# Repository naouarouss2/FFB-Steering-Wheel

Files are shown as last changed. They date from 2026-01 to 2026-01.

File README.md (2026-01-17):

# DIY FFB Steering Wheel
## What is it ?
A Force Feedback Wheelbase is a device used in car, truck, bus, or any other 3+ wheeled vehicle (as motorcycles require something different).

The difference between it and a standard game controller is, as the name suggests : **Force Feedback**

Force Feedback is what will create a physical connection between you and the game/simulator you're playing. It will allow you to feel every bump, road imperfection, steering stiffness, vibration... as if you're driving in real life.

## Features
-  **Direct drive**, making it very silent, providing the most accurate and lossless feedback
-  **12-15Nm Force Feedback** (**5.7-7.1x** more powerful than the Logitech G29)
-  **12 Programmable buttons** (Depends on the wheel attached)
-  **Auto center**
-  **0.01125° sensitivity**, making it comparable to some high-end wheelbases on the market

## Why do I want to make it ?
I have always wanted to have a simracing setup. Whenever I go to a mall or a gaming café and see a simracing setup, I run like a kid to try it.

I once tried a professional direct drive setup with a motion setup, and this really made me more excited about simracing.

The problem is that the only decent wheelbase available in Tunisia is the Logitech G29 family. They are pretty nice, but overpriced in Tunisia, and it really didn't really fill my heart and satisfy my requirements.

So I wanted to build my own wheelbase, tweaked to my likings and preferences, with endless upgrading and tuning options.

## 3D Design
I designed everything inside Solidworks, as I am pretty familiar with it, and I already have the CSWA certification.
I divided the design in 2 parts :
-  First, the wheelbase sub-assembly :

| **Full design** | **Aluminium machined parts** | **3D Printed parts** | **Commercial parts** |
|---|---|---|---|
||||

-  Next, the steering wheel sub-assembly

| **Full design** | **Aluminium machined parts** | **3D Printed parts** | **Commercial parts** |
|---|---|---|---|
|||||

And here are pictures of the finished product !


## Wheelbase PCB
To minimize wiring and make things simpler and cleaner inside, I made a PCB for the wheelbase

| **3D View** | **PCB Routing View** | **Schematics** | 
|---|---|---|
||||

## Wiring Diagrams
### Wheelbase wiring diagram
fb58e3fb-e4d4-41d1-b4ad-96e4c3caae32
### Steering wheel wiring diagram (made on KiCad, but no PCB)


## BOM

|Type |Component name |Product description |Shop / Manufacturer |Local|URL |Unit price|Shipping|Product Amount|Product Total (excluding shipping)|Product Total (with shipping)|
|---|---|---|---|-----|---|---|---|---|---|---|
|Commercial parts |20*20mm Aluminium Profile|Used to make the wheelbase frame |Seli |Yes  |https://seli.tn/product/20x20-profile-aluminium-industriel-dk/ |15,6 |0 |1 |15,6 |15,6 |
| |40*20mm Aluminium Profile|Used to make the wheelbase frame |Seli |Yes  |https://seli.tn/product/20x40-profile-aluminium-industriel-r6/ |22,5 |0 |1 |22,5 |22,5 |
| |SK16 Brackets |Used to mount the motor in place |Seli |Yes  |https://seli.tn/product/sk16-support-d-arbre-en-aluminium-diam-16/ |3,11 |0 |2 |6,22 |6,22 |
| |UFL004 Bearings |Used to guide the shaft in rotation |Aliexpress |No |https://ar.aliexpress.com/item/1005007098430647.html |17,9 |0 |1 |17,9 |17,9 |
| |ODESC 52V Driver |Used to drive the motor and process FFB Logic |Aliexpress |No |https://ar.aliexpress.com/item/1005005763345874.html |78 |13,2 |1 |78 |91,2 |
| |STM32H743VIT6 Board |Used to control the ODESC board along with the game inputs |Aliexpress |No |https://ar.aliexpress.com/item/1005009563874211.html |11,55 |4,05 |1 |11,55 |15,6 |
| |2000PPR Rotary Encoder |Used to determine the steering wheel's position |Aliexpress |No |https://ar.aliexpress.com/item/1005004387342695.html |15,35 |7,82 |1 |15,35 |23,17 |
| |30-tooth 30mm pulley |Used to tie the encoder's shaft to the steering wheel shaft |Aliexpress |No |https://ar.aliexpress.com/item/1005008678109995.html |4,67 |0 |1 |4,67 |4,67 |
| |Quick release mechanism  |Used to mount the steering wheel to the wheelbase |Aliexpress |No |https://ar.aliexpress.com/item/1005009121231549.html |62,86 |0 |1 |62,86 |62,86 |
| |GX12 Connector kit (M/F) |Used to connect input peripherals to the wheelbase |Tunisian Smart Innovation|Yes  |https://tuni-smart-innovation.com/products/connecteur-male-et-femelle-gx12-4-broches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 |1,49 |0 |5 |7,45 |7,45 |
| |120mm Fan |Used to cool the wheelbase's electronics |2BTrading |Yes  |https://2btrading.tn/ventilateur-radiateur/2391-ventilateur-dc12v-034a-12x12x38cm.html |10,73 | |1 |10,73 |10,73 |
| |XT60M connector |Used to power the wheelbase |Cothings |Yes  |https://cothings.net/products/connecteur-amass-xt60e-m-male |1,73 |0 |1 |1,73 |1,73 |
| |Endstop switch |Game inputs |Cothings |Yes  |https://cothings.net/products/copie-de-capteur-de-temperature-thermistance-ntc-100k-ntc-mf52at-1 |0,45 |0 |2 |0,9 |0,9 |
| |Pushbutton |Game inputs |Cothings |Yes  |https://cothings.net/products/mini-bouton-poussoir-rond-a-reinitialisation-automatique-bleu-etanche-pbs-33b-12mm-2-broches |0,86 |0 |8 |6,88 |6,88 |
| |Hall effect sensor |Used to calibrate the wheel's initial position |Cothings |Yes  |https://cothings.net/products/ky-024-capteur-a-effet-hall-analogique-pour-vitesse-et-comptage |1,55 |0 |1 |1,55 |1,55 |
| |36V 500W Power supply |Used to power the wheelbase |Aliexpress |No |https://ar.aliexpress.com/item/1005003923590693.html |50,53 |10,49 |1 |50,53 |61,02 |
| |GT2-6 400mm belt |Used to connect the shaft pulley to the encoder pulley |2BTrading |Yes  |Courroie GT2-6 400mm |3 |0 |1 |3 |3 |
| |Seed XIAO RP2040 |Microcontroller for the steering wheel |Aliexpress |No |https://ar.aliexpress.com/item/1005003682505451.html |4,78 |4,52 |1 |4,78 |9,3 |
| |Steering Wheel |The actual steering wheel |Aliexpress |No |https://ar.aliexpress.com/item/1005009791304312.html |25,99 |42,53 |1 |25,99 |68,52 |
| |TJA1051 |CAN transceiver |Aliexpress |No |https://ar.aliexpress.com/item/1005005569468051.html |4,1 |0 |1 |4,1 |4,1 |
| |12V Buck Converter |Used to power the fan |Aliexpress |No |https://ar.aliexpress.com/item/1005008597548688.html |2,6 |7,28 |1 |2,6 |12,48 |
| |5V Buck Converter |Used to power the MCU and other peripherals |Aliexpress |No |https://ar.aliexpress.com/item/1005008597548688.html |2,6 | |1 |2,6 | |
| |USB-C Female Connector |Used to connect the wheelbase to the computer |Aliexpress |No |https://ar.aliexpress.com/item/1005009695057393.html |11,62 |0 |1 |11,62 |11,62 |
| |USB-C 90° cable |Used to transfer the USB connection from the PCB to the external connector|Aliexpress |No |https://ar.aliexpress.com/item/1005002708307702.html |6,4 |4,79 |1 |6,4 |11,19 |
| |USB-C Breakout Board | |Aliexpress |No |https://ar.aliexpress.com/item/1005004807492800.html |4,19 |0 |1 |4,19 |4,19 |
| |JST-XH 4 Pin Connector |Used to make cable connections easier |Tunisian Smart Innovation|Yes  |https://tuni-smart-innovation.com/products/connecteur-jst-xh2-54-4-broches-male-femelle-avec-cable-de-20-cm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 |0,7 |0 |1 |0,7 |0,7 |
| |JST-XH 3 Pin Connector |Used to make cable connections easier |Tunisian Smart Innovation|Yes  |https://tuni-smart-innovation.com/products/connecteur-jst-xh2-54-3-broches-male-femelle-avec-cable-de-20-cm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|0,62 |0 |1 |0,62 |0,62 |
| |JST-XH 2 Pin Connector |Used to make cable connections easier |Tunisian Smart Innovation|Yes  |https://tuni-smart-innovation.com/products/connecteur-jst-xh-2-broches-male-femelle-avec-cable-de-20-cm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 |0,49 |0 |1 |0,49 |0,49 |
| |M2X10 Screw |Screw diameter = 2mm, length = 10mm |Already have | |N/A |0 |0 |4 |0 |0 |
| |M3x10 Screw |Screw diameter = 3mm, length = 10mm |Already have | |N/A |0 |0 |8 |0 |0 |
| |M3x16 Screw |Screw diameter = 3mm, length = 16mm |Already have | |N/A |0 |0 |10 |0 |0 |
| |M4x8 Screw |Screw diameter = 4mm, length = 8mm |Already have | |N/A |0 |0 |8 |0 |0 |
| |M4x16 Screw |Screw diameter = 4mm, length = 16mm |Already have | |N/A |0 |0 |4 |0 |0 |
| |M5x16 Screw |Screw diameter = 5mm, length = 16mm |Already have | |N/A |0 |0 |6 |0 |0 |
| |M5x36 Screw |Screw diameter = 5mm, length = 36mm |Already have | |N/A |0 |0 |4 |0 |0 |
| |M5x50 Screw |Screw diameter = 5mm, length = 50mm |Already have | |N/A |0 |0 |6 |0 |0 |
| |M6x20 Screw |Screw diameter = 6mm, length = 20mm |Already have | |N/A |0 |0 |4 |0 |0 |
| |M10x16 Screw |Screw diameter = 10mm, length = 16mm |Already have | |N/A |0 |0 |2 |0 |0 |
| |M3 Nut |Nut diameter = 3mm |Already have | |N/A |0 |0 |4 |0 |0 |
| |M10 Nut |Nut diameter = 10mm |Already have | |N/A |0 |0 |2 |0 |0 |
| |M3 Aluminium Profile Nut |Nut for aluminium profiles, diameter = 3mm |Seli |Yes  |https://seli.tn/product/ecrou-marteau/ |0,1 |0 |4 |0,4 |0,4 |
| |M4 Aluminium Profile Nut |Nut for aluminium profiles, diameter = 4mm |Seli |Yes  |https://seli.tn/product/ecrou-marteau/ |0,1 |0 |8 |0,8 |0,8 |
| |M5 Aluminium Profile Nut |Nut for aluminium profiles, diameter = 5mm |Seli |Yes  |https://seli.tn/product/ecrou-marteau/ |0,1 |0 |4 |0,4 |0,4 |
| |M6 Aluminium Profile Nut |Nut for aluminium profiles, diameter = 6mm |Seli |Yes  |https://seli.tn/product/ecrou-marteau/ |0,1 |0 |4 |0,4 |0,4 |
| |Table clamps (x2) |Used to mount the wheelbase on the table |Aliexpress |No |https://ar.aliexpress.com/item/1005006458478718.html |47,8 |8,28 |1 |47,8 |56,08 |
| |Hoverboard motor |Used to provide force feedback |Facebook Marketplace |Yes  |N/A |19 |0 |1 |19 |19 |
| |TOTAL | | | | | | | |450,31 |553,27 |
|PCB |Wheelbase PCB |Holds the various electronic components without the need for wiring |JLC PCB |No |N/A |2 |21,91 |1 |2 |21,91 |
|Aluminium machined parts|Front plate | |JLC CNC |No |N/A |8,72 |49,48 |1 |8,72 |72,77 |
| |Back plate | |JLC CNC |No |N/A |10,63 | |1 |10,63 | |
| |Paddle (x2) | |JLC CNC |No |N/A |3,94 | |1 |3,94 | |
|GRAND TOTAL | | | | | | | | |475,6 |647,95 |

This table format above is slightly different from what I originally made, so to understand it better, I would recommend

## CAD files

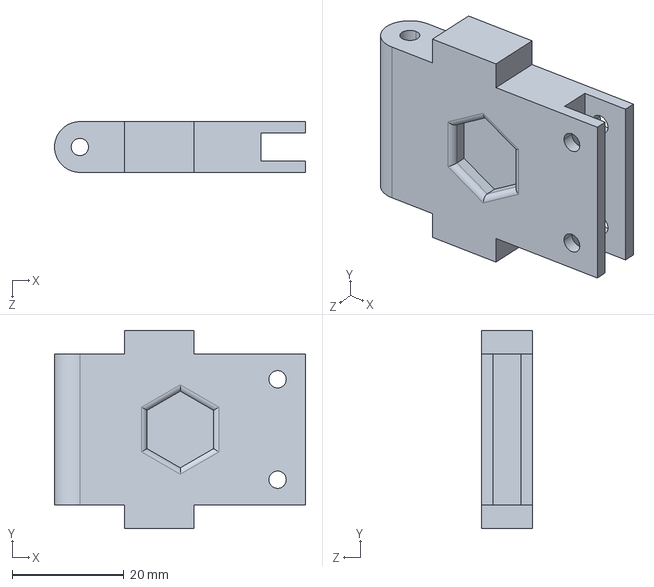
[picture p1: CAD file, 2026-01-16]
CAD/Steering Wheel/3D Printed parts/Paddle Holder.STEP
45.0 x 35.5 x 9.10 mm

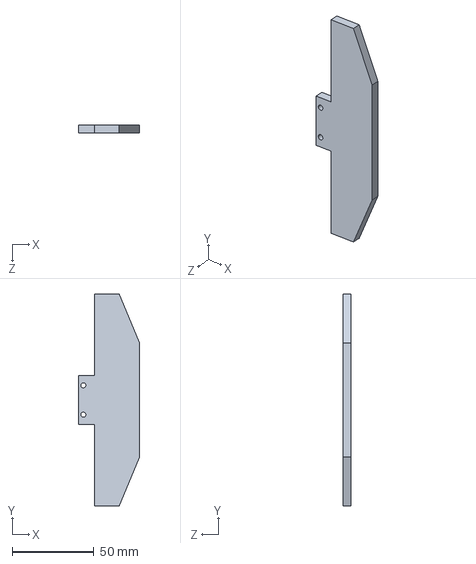
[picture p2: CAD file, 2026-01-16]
CAD/Steering Wheel/Aluminium machined parts/Paddle.STEP
37.5 x 130.0 x 5.00 mm

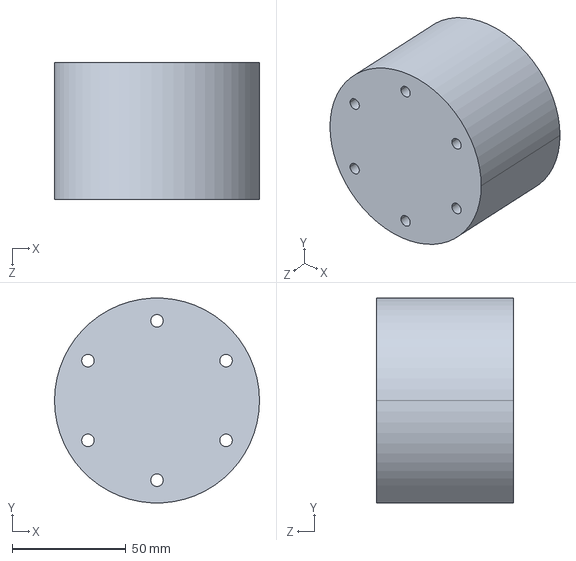
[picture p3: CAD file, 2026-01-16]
CAD/Steering Wheel/Commercial parts/QR Sample.STEP
90.0 x 89.9 x 60.0 mm

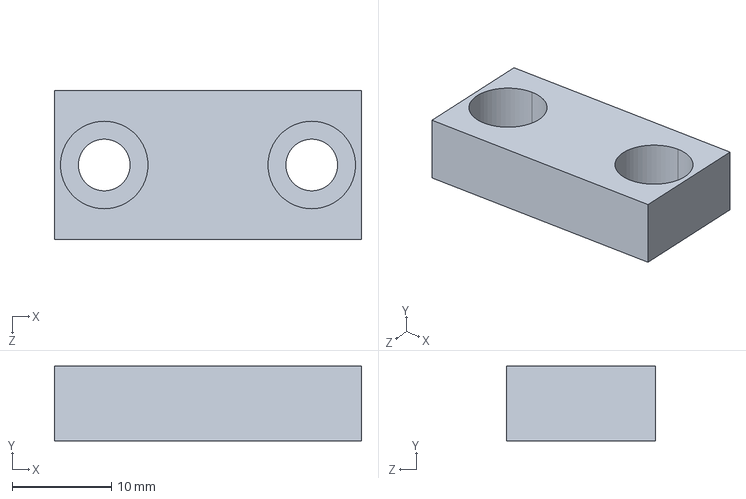
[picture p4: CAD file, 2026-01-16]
CAD/Wheelbase/3D Printed parts/Clamp Surface Flattener.STEP
30.9 x 7.50 x 15.0 mm

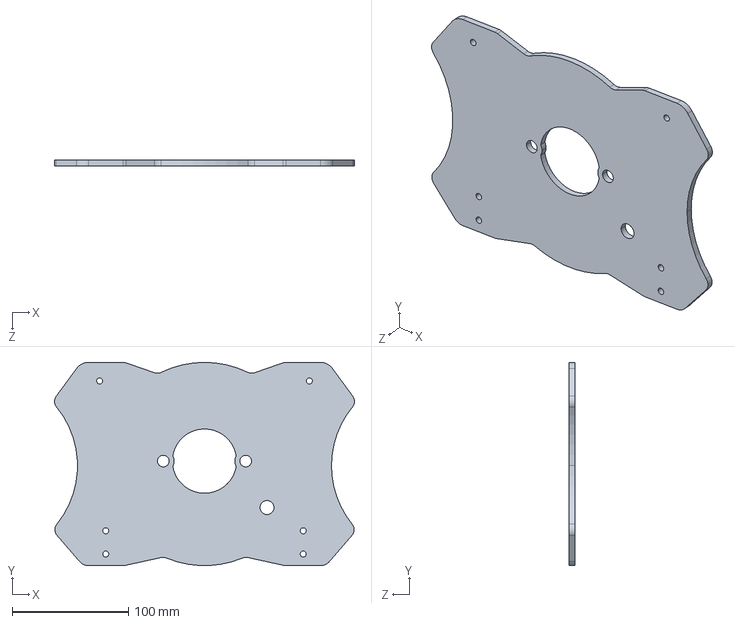
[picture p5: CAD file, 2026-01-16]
CAD/Wheelbase/Aluminium machined parts/Front plate.STEP
258.3 x 175.0 x 5.00 mm

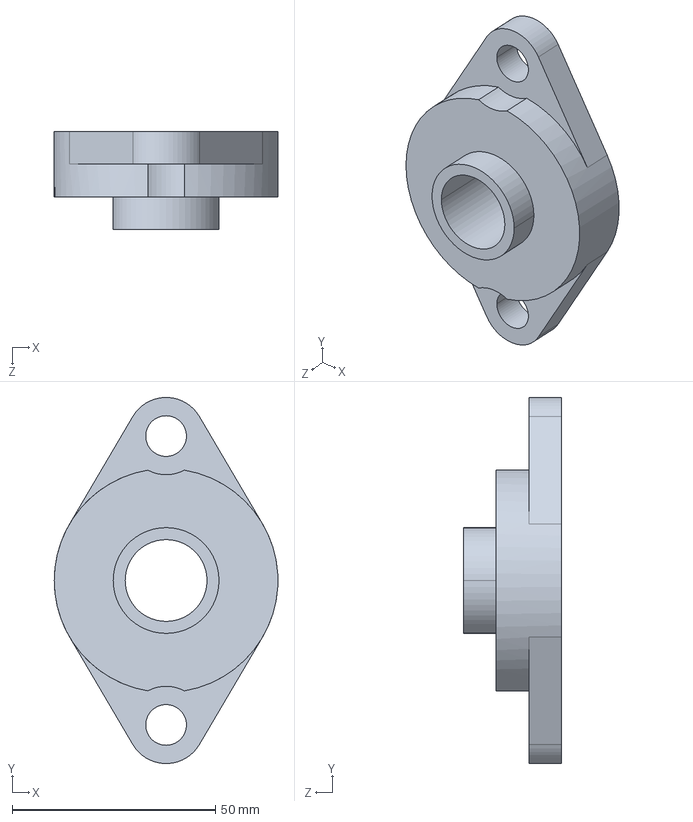
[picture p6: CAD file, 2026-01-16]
CAD/Wheelbase/Commercial parts/KFL004.STEP
55.0 x 90.0 x 24.0 mm

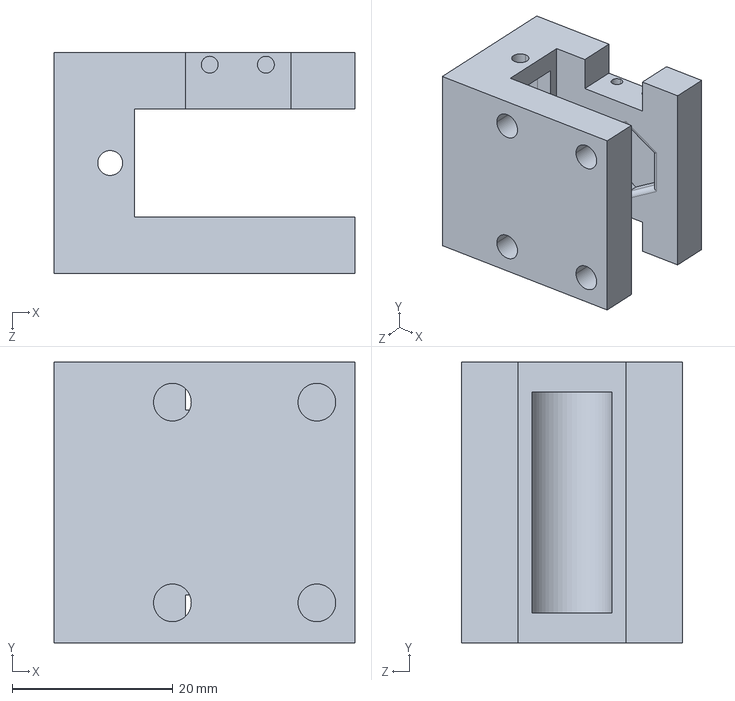
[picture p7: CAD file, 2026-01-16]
CAD/Steering Wheel/3D Printed parts/Paddle Shifter Mount.STEP
37.5 x 35.0 x 27.5 mm

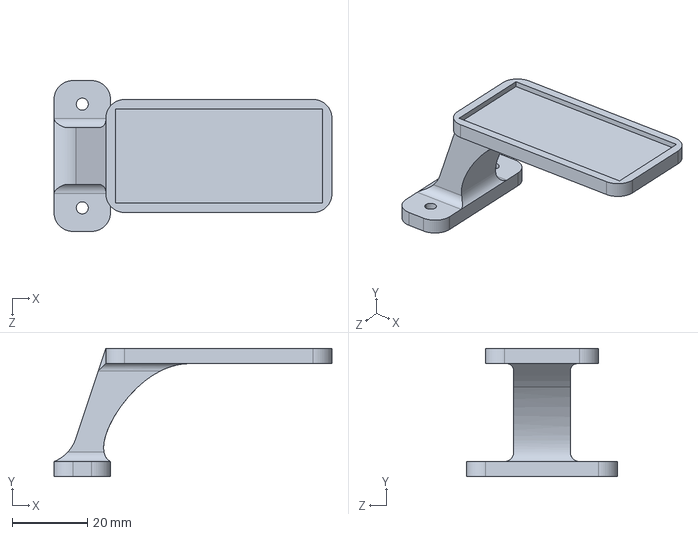
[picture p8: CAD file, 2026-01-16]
CAD/Wheelbase/3D Printed parts/Hall Eff Sensor Mount.STEP
73.8 x 34.0 x 40.0 mm

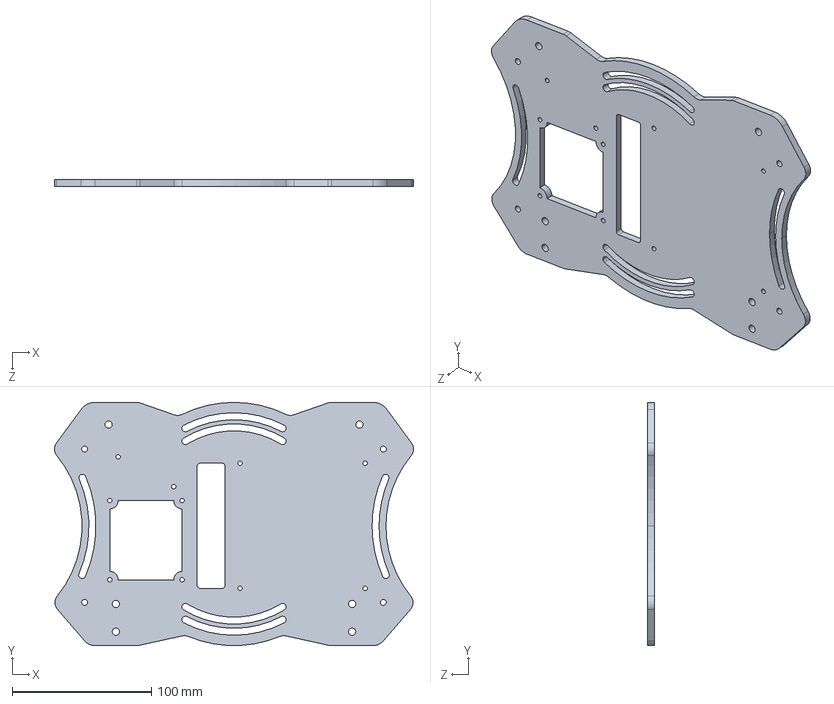
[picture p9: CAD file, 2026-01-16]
CAD/Wheelbase/Aluminium machined parts/Back plate.STEP
258.3 x 175.0 x 5.00 mm

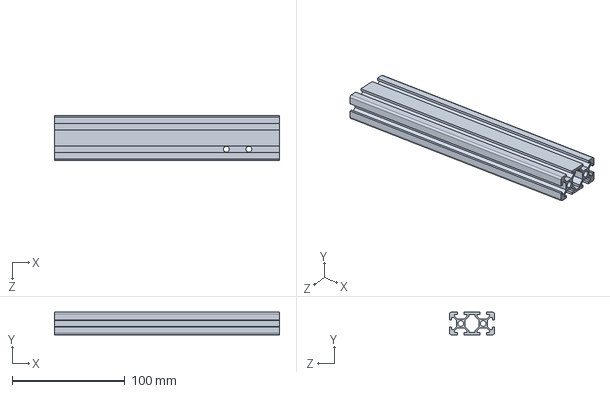
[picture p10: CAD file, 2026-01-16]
CAD/Wheelbase/Commercial parts/Side 2040 profile.STEP
200.0 x 20.0 x 40.0 mm

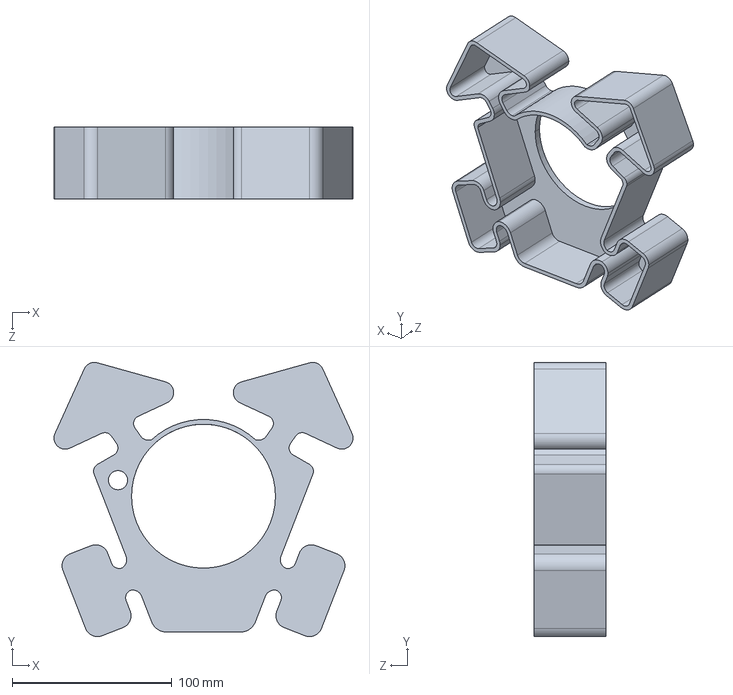
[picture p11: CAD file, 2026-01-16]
CAD/Steering Wheel/3D Printed parts/Back Enclosure.STEP
187.0 x 171.5 x 45.0 mm

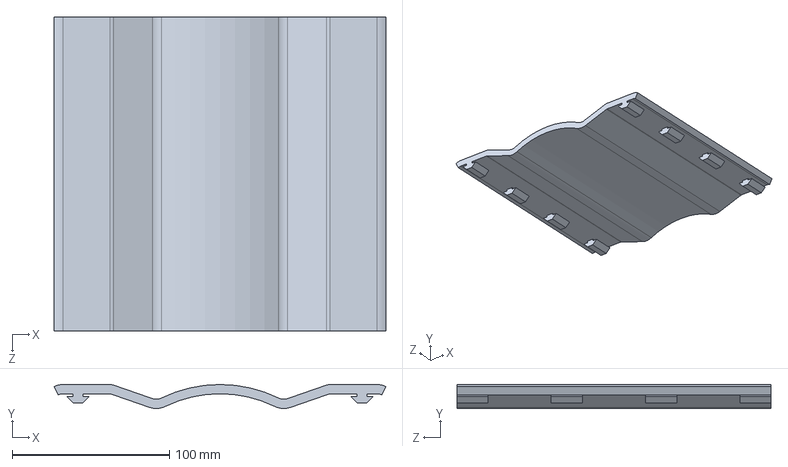
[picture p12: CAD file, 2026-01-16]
CAD/Wheelbase/3D Printed parts/Top cover.STEP
211.1 x 15.3 x 200.0 mm

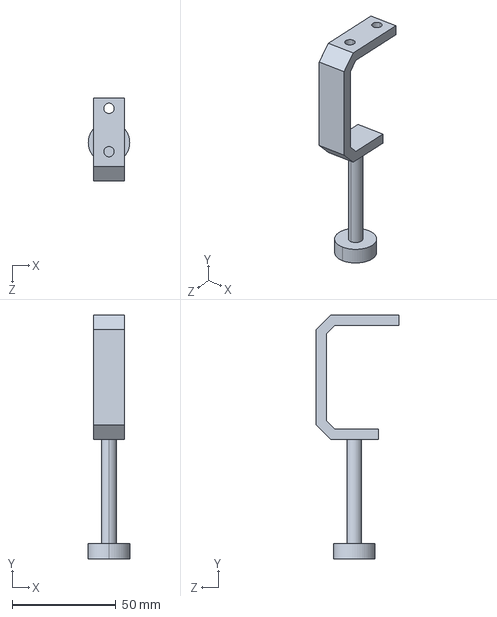
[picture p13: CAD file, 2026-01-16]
CAD/Wheelbase/Commercial parts/Clamp Sample.STEP
20.0 x 117.5 x 40.0 mm

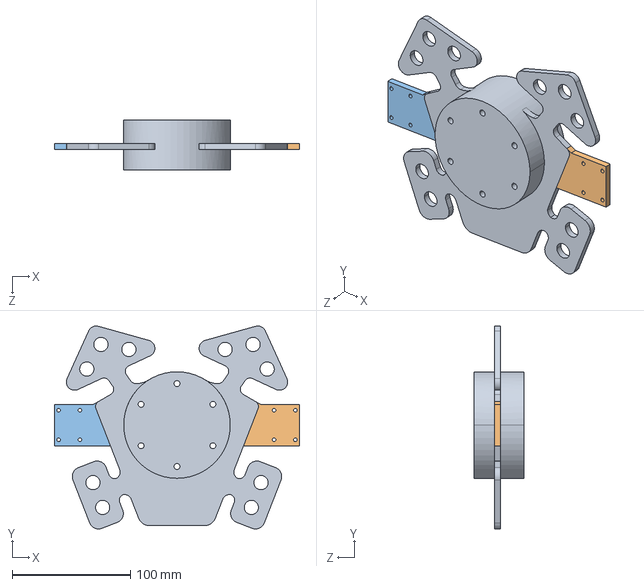
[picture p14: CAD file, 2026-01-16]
CAD/Steering Wheel/3D Printed parts/Front.STEP
207.0 x 171.5 x 42.5 mm

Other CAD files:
CAD/Wheelbase/3D Printed parts/Bottom cover.STEP
CAD/Wheelbase/Commercial parts/30T Pulley.STEP
CAD/Wheelbase/3D Printed parts/Shaft Pulley.STEP
CAD/Wheelbase/Commercial parts/SK16.STEP
CAD/Steering Wheel/Commercial parts/Files from Grabcad/GX12M.step
CAD/Steering Wheel/Commercial parts/Files from Grabcad/Limit_Switch.STEP
CAD/Steering Wheel/Commercial parts/Files from Grabcad/ic184-thread.STEP
CAD/Steering Wheel/Commercial parts/Screws/M2x10.STEP
CAD/Steering Wheel/Commercial parts/Screws/M3x10.STEP
CAD/Steering Wheel/Commercial parts/Screws/M5x50.STEP
CAD/Wheelbase/3D Printed parts/Back cover.STEP
CAD/Wheelbase/3D Printed parts/Encoder Mount V2.STEP
CAD/Wheelbase/3D Printed parts/Left Cover.STEP
CAD/Wheelbase/3D Printed parts/QR Adapter.STEP
CAD/Wheelbase/3D Printed parts/Right cover.STEP
CAD/Wheelbase/3D Printed parts/Riser.STEP
CAD/Wheelbase/3D Printed parts/Shaft Mount.STEP
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

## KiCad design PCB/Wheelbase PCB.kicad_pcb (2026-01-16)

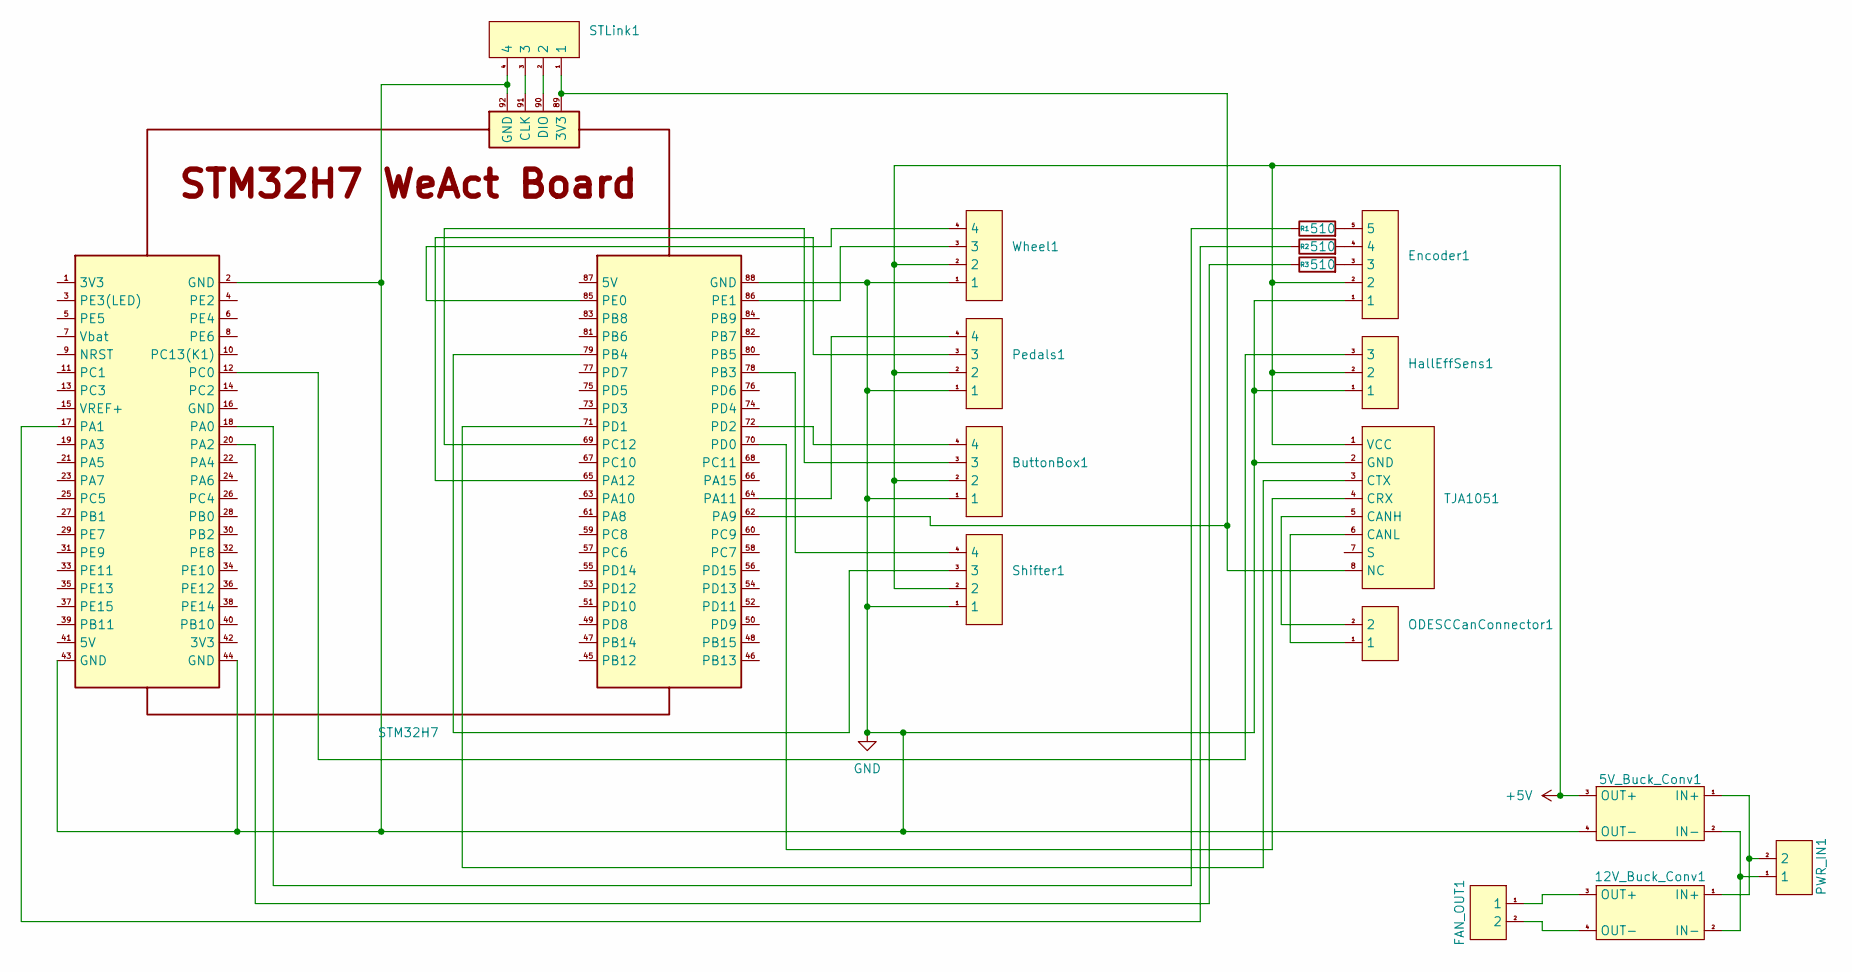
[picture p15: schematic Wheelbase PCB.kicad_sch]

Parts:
5V_Buck_Conv1, 12V_Buck_Conv1: Buck Converter
ButtonBox1: JST_XH_B4B-XH-A_1x04_P2.50mm_Vertical
Encoder1: JST_XH_B5B-XH-A_1x05_P2.50mm_Vertical
FAN_OUT1: JST_XH_B2B-XH-A_1x02_P2.50mm_Vertical
HallEffSens1: JST_XH_B3B-XH-A_1x03_P2.50mm_Vertical
ODESCCanConnector1: JST_XH_B2B-XH-A_1x02_P2.50mm_Vertical
PWR_IN1: JST_XH_B2B-XH-A_1x02_P2.50mm_Vertical
Pedals1: JST_XH_B4B-XH-A_1x04_P2.50mm_Vertical
R1, R2, R3: 510; R_Axial_DIN0207_L6.3mm_D2.5mm_P10.16mm_Horizontal
STLink1: JST_XH_B4B-XH-A_1x04_P2.50mm_Vertical
STM32H7: WeAct Board
Shifter1: JST_XH_B4B-XH-A_1x04_P2.50mm_Vertical
TJA1051: TJA1051 Board
Wheel1: JST_XH_B4B-XH-A_1x04_P2.50mm_Vertical

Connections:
+5V: 5V_Buck_Conv1.3 (OUT+), ButtonBox1.2, Encoder1.2, HallEffSens1.2, Pedals1.2, Shifter1.2, TJA1051.1 (VCC), Wheel1.2
GND: 5V_Buck_Conv1.4 (OUT-), ButtonBox1.1, Encoder1.1, HallEffSens1.1, Pedals1.1, STLink1.4, STM32H7.2 (GND), STM32H7.43 (GND), STM32H7.44 (GND), STM32H7.88 (GND), STM32H7.92 (GND), Shifter1.1, TJA1051.2 (GND), Wheel1.1
unnamed: 5V_Buck_Conv1.1 (IN+), 12V_Buck_Conv1.1 (IN+), PWR_IN1.2
unnamed: 5V_Buck_Conv1.2 (IN-), 12V_Buck_Conv1.2 (IN-), PWR_IN1.1
unnamed: 12V_Buck_Conv1.3 (OUT+), FAN_OUT1.1
unnamed: 12V_Buck_Conv1.4 (OUT-), FAN_OUT1.2
unnamed: Encoder1.3, R3.2
unnamed: Encoder1.4, R2.2
unnamed: Encoder1.5, R1.2
unnamed: STLink1.3, STM32H7.91 (CLK)
unnamed: STLink1.2, STM32H7.90 (DIO)
unnamed: R1.1, STM32H7.18 (PA0)
unnamed: R2.1, STM32H7.17 (PA1)
unnamed: R3.1, STM32H7.20 (PA2)
unnamed: STLink1.1, STM32H7.62 (PA9), STM32H7.89 (3V3), TJA1051.8 (NC)
unnamed: Pedals1.4, STM32H7.64 (PA11)
unnamed: Pedals1.3, STM32H7.65 (PA12)
unnamed: STM32H7.78 (PB3), Shifter1.4
unnamed: STM32H7.79 (PB4), Shifter1.3
unnamed: HallEffSens1.3, STM32H7.12 (PC0)
unnamed: ButtonBox1.3, STM32H7.69 (PC12)
unnamed: STM32H7.70 (PD0), TJA1051.4 (CRX)
unnamed: STM32H7.71 (PD1), TJA1051.3 (CTX)
unnamed: ButtonBox1.4, STM32H7.72 (PD2)
unnamed: STM32H7.85 (PE0), Wheel1.4
unnamed: STM32H7.86 (PE1), Wheel1.3
unnamed: ODESCCanConnector1.2, TJA1051.5 (CANH)
unnamed: ODESCCanConnector1.1, TJA1051.6 (CANL)

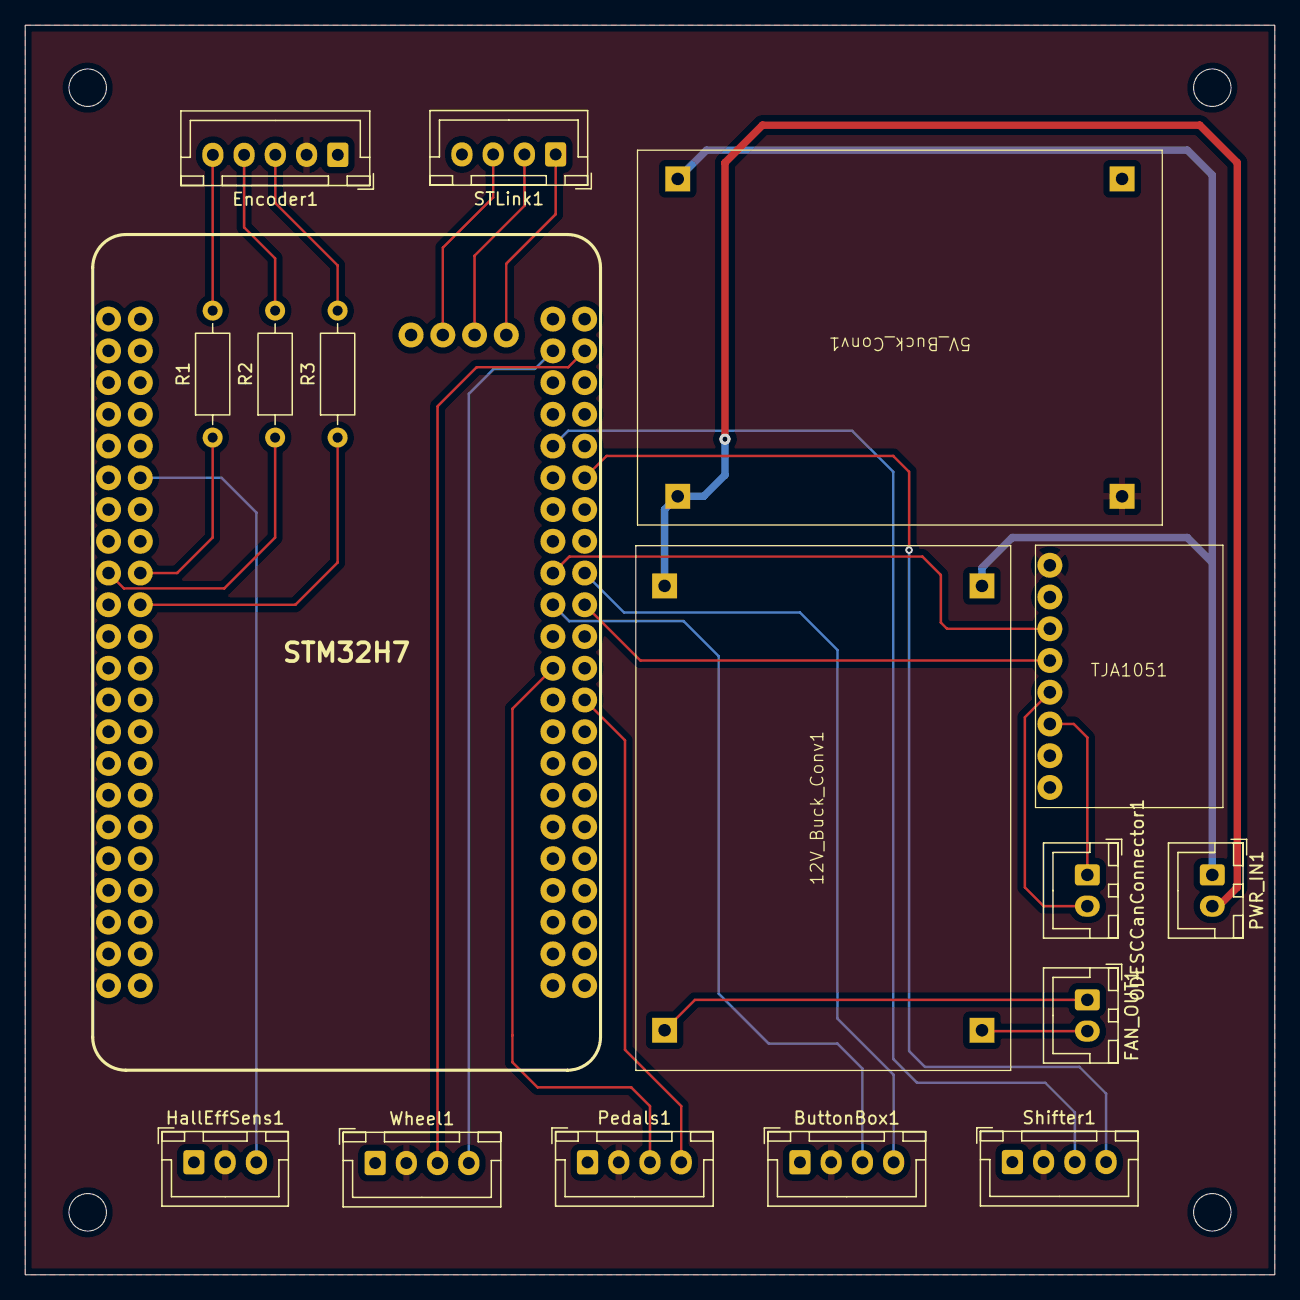
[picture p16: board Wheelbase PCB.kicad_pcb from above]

Board: 4 copper layers, 100.0 x 100.0 mm, 17 parts (0 on the bottom side), 28 nets.

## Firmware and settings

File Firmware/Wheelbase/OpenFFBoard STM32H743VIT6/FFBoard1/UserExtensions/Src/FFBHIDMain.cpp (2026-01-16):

/*
 * FFBWheel.cpp
 *
 *  Created on: 31.01.2020
 *      Author: Yannick / Lidders
 */

#include <FFBHIDMain.h>
#include "voltagesense.h"
#include "hid_device.h"
#include "tusb.h"
#include "usb_hid_ffb_desc.h"

#include "cmsis_os.h"
extern osThreadId_t defaultTaskHandle;

//////////////////////////////////////////////


/**
 * setFFBEffectsCalc must be called in constructor of derived class to finish the setup
 */
FFBHIDMain::FFBHIDMain(uint8_t axisCount) :
		Thread("FFBMAIN", 256, 30),
		SelectableInputs(ButtonSource::all_buttonsources,AnalogSource::all_analogsources),
		axisCount(axisCount)
{

	restoreFlashDelayed(); // Load parameters
	registerCommands();

}

/**
 * MUST be called in the constructor of the derived class.
 * This finishes the construction because the constructor of this class will be called before the ffb and effects calc
 * objects are created in the derived class.
 */
void FFBHIDMain::setFFBEffectsCalc(std::shared_ptr<EffectsControlItf> ffb,std::shared_ptr<EffectsCalculator> effects_calc){
	this->ffb = ffb;
	this->effects_calc = effects_calc;
	axes_manager = std::make_unique<AxesManager>(&control,effects_calc);
	axes_manager->setAxisCount(axisCount);
	this->Start();
}


FFBHIDMain::~FFBHIDMain() {
	clearBtnTypes();
}

/**
 * Read parameters from flash and restore settings
 */
void FFBHIDMain::restoreFlash(){

	Flash_Read(ADR_FFBWHEEL_BUTTONCONF, &this->btnsources);
	setBtnTypes(this->btnsources);

	Flash_Read(ADR_FFBWHEEL_ANALOGCONF, &this->ainsources);
	setAinTypes(this->ainsources);

	uint16_t conf1 = 0;
	if(Flash_Read(ADR_FFBWHEEL_CONF1,&conf1)){
		uint8_t rateidx = conf1 & 0x3;
		setReportRate(rateidx);
	}

}
/**
 * Save parameters to flash
 */
void FFBHIDMain::saveFlash(){

	Flash_Write(ADR_FFBWHEEL_BUTTONCONF,this->btnsources);
	Flash_Write(ADR_FFBWHEEL_ANALOGCONF,this->ainsources);

	uint8_t conf1 = 0;
	conf1 |= usb_report_rate_idx & 0x3;
	Flash_Write(ADR_FFBWHEEL_CONF1,conf1);
}



void FFBHIDMain::Run(){
#ifdef E_STOP_Pin
	bool estopState = HAL_GPIO_ReadPin(E_STOP_GPIO_Port, E_STOP_Pin) == GPIO_PIN_RESET;
	if(estopState){ // Estop pressed at startup
		emergencyStop(!estopState);
//		control.emergency = true; // Immediately enter emergency state but without notifying other classes yet
		lastEstop = HAL_GetTick();
	}
#endif
	while(true){
		Delay(1);
		updateControl();
	}
}

/**
 * Main update loop
 */
void FFBHIDMain::updateControl(){
	if(control.request_update_disabled) {
		//logSerial("request update disabled");
		control.update_disabled = true;
		control.request_update_disabled = false;

	}
	if(control.update_disabled){
		//logSerial("Update disabled");
		return;
	}

	if(control.resetEncoder){
		control.resetEncoder = false;
		axes_manager->resetPosZero();
	}

	//debugpin.set();
	axes_manager->update();

	if(++report_rate_cnt >= usb_report_rate){
		report_rate_cnt = 0;
		this->send_report();
	}
	if(!control.emergency){
		axes_manager->updateTorque();

	}else{
		pulseClipLed();
	}
	//debugpin.reset();
}


uint32_t FFBHIDMain::getRate() {
	return this->ffb->getRate();
}

bool FFBHIDMain::getFfbActive(){
	return this->ffb->getFfbActive();
}

/**
 * Sends periodic gamepad reports of buttons and analog axes
 */
void FFBHIDMain::send_report(){
	// Check if HID command interface wants to send something and allow that if we did not skip too many reports
	if(!tud_hid_n_ready(0) ||  ((reportSendCounter++ < usb_report_rate*2) && this->hidCommands->waitingToSend())){
		return;
	}
	//Try semaphore
//	if(!sourcesSem.Take(10)){
//		return;
//	}
	// Read buttons
	reportHID.buttons = 0; // Reset buttons

	uint64_t b = 0;
	SelectableInputs::getButtonValues(b);
	reportHID.buttons = b;

	// Encoder
	//axes_manager->addAxesToReport(analogAxesReport, &count);

	std::vector<int32_t>* axes = axes_manager->getAxisValues();
	uint8_t count = 0;
	for(auto val : *axes){
		setHidReportAxis(&reportHID,count++,val);
	}

	// Fill remaining values with analog inputs
	axes = SelectableInputs::getAnalogValues();
	for(int32_t val : *axes){
		if(count >= analogAxisCount)
			break;
		setHidReportAxis(&reportHID,count++,val);
	}
//	sourcesSem.Give();
	// Fill rest
	for(;count<analogAxisCount; count++){
		setHidReportAxis(&reportHID,count,0);
	}


	/*
	 * Only send a new report if actually changed since last time or timeout and hid is ready
	 */
	if( (reportSendCounter > 100/usb_report_rate || (memcmp(&lastReportHID,&reportHID,sizeof(reportHID_t)) != 0) ))
	{


	tud_hid_report(0, reinterpret_cast<uint8_t*>(&reportHID), sizeof(reportHID_t));
	lastReportHID = reportHID;
	reportSendCounter = 0;

	}

}

/**
 * Changes the hid report rate based on the index for usb_report_rates
 */
void FFBHIDMain::setReportRate(uint8_t rateidx){
	rateidx = clip<uint8_t,uint8_t>(rateidx, 0,sizeof(usb_report_rates));
	usb_report_rate_idx = rateidx;
	usb_report_rate = usb_report_rates[rateidx]*HID_BINTERVAL;
}

/**
 * Generates the speed strings to display to the user
 */
std::string FFBHIDMain::usb_report_rates_names() {
		std::string s = "";
		for(uint8_t i = 0 ; i < sizeof(usb_report_rates);i++){
			s += std::to_string(1000/(HID_BINTERVAL*usb_report_rates[i])) + "Hz:"+std::to_string(i);
			if(i < sizeof(usb_report_rates)-1)
				s += ",";
		}
		return s;
	}

void FFBHIDMain::emergencyStop(bool reset){
	control.emergency = !reset;
	axes_manager->emergencyStop(reset);
}

//void FFBHIDMain::timerElapsed(TIM_HandleTypeDef* htim){
//
//}


/**
 * USB unplugged
 * Deactivates FFB
 */
void FFBHIDMain::usbSuspend(){
	if(control.usb_disabled)
		return;
	control.usb_disabled = true;
	ffb->stop_FFB();
	ffb->reset_ffb(); // Delete all effects
	axes_manager->usbSuspend();
}

/**
 * USB plugged in
 */
void FFBHIDMain::usbResume(){
#ifdef E_STOP_Pin
	if(control.emergency && HAL_GPIO_ReadPin(E_STOP_GPIO_Port, E_STOP_Pin) != GPIO_PIN_RESET){ // Reconnected after emergency stop
		control.emergency = false;
	}
#endif
	control.usb_disabled = false;
	axes_manager->usbResume();
}


// External interrupt pins
void FFBHIDMain::exti(uint16_t GPIO_Pin){
	if(GPIO_Pin == BUTTON_A_Pin){
		// Button down?
		if(HAL_GPIO_ReadPin(BUTTON_A_GPIO_Port, BUTTON_A_Pin)){
			this->control.resetEncoder = true;
		}
	}
#ifdef E_STOP_Pin
	if(GPIO_Pin == E_STOP_Pin){ // Emergency stop. low active
//		if(HAL_GPIO_ReadPin(E_STOP_GPIO_Port, E_STOP_Pin) == GPIO_PIN_RESET){
		bool estopPinState = HAL_GPIO_ReadPin(E_STOP_GPIO_Port, E_STOP_Pin) == GPIO_PIN_RESET;
		if(HAL_GetTick()-lastEstop > 1000 && estopPinState != this->control.emergency){ // Long debounce
			lastEstop = HAL_GetTick();
			if(estopPinState){
				emergencyStop(false);
			}else if(allowEstopReset){
				emergencyStop(true);
			}

		}
//		}
	}
#endif
}

/*
 * Error handling
 */
void FFBHIDMain::errorCallback(const Error &error, bool cleared){
	if(error.type == ErrorType::critical){
		if(!cleared){
			this->emergencyStop(true);
		}
	}
	if(error.code == ErrorCode::emergencyStop){
		this->emergencyStop(cleared); // Clear Estop
	}
	if(!cleared){
		pulseErrLed();
	}
}
